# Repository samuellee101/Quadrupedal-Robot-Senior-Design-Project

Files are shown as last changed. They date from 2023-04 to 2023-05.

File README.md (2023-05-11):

# Quadrupedal Robot with the aim of Obstacle Avoidance using Artificial Intelligence
UTRGV - University of Texas Rio Grande Valley

Hello, my name is Samuel Lee, and together with my fellow teammmates Ryunghoon Ahn, and Christian Valdes, we aimed to have a quadrupedal robot walking by the end of our senior design project. The eventual goal of this project was to have a walking quadrupedal robot that moves using Artificial Intelligence, and is able to avoid obstacles (walls, buckets, basketballs), however, for the purposes of our senior design project, we wanted a walking quadrupdal robot.

This is meant to be a repository to show to future students working on this project, with helpful files to guide these students.

The quadrupedal robot was built using a combination of 3D printed parts using UTRGV's engineering building print labs, servos/wires/Jetson Nano purchased online, and was constructed in the Artificial Intelligence lab at UTRGV.

Ryunghoon Ahn was responsible for the physical construction of the robot. This includes soldering/screwing parts and ordering electrical parts online.

The file 'gazebo/spot_mini_mini' has work that Christian and Ryunghoon did in order to make the robot run in simulations.

The file 'gyroscope' details work that Samuel did in order to get the gyroscope up and running.

The file 'midterm-presentation' shows what we presented during our midterm presentations, and the powerpoint within details our progress halfway through this project. Joint Christian/Samuel effort.

The file '3D-printed-instructions' details work that Samuel did in order to get the 3D printed parts necessary for the project.

'End-of-Semester-Deliverables' has our final report and final presentation.

Christian and Ryunghoon are responsible for the simulation aspect of this project.

The robot itself is able to move its legs with the help of the servo. Video/Images will be included in the final presentation.

We would like to thank Christian Narcia from the Artificial Intelligence labs for the files found in 'revised-stl-parts.'

Special thanks to Dr. Dongchul Kim for being our project overseer, and Dr. Noe Vargas for his patience at the Makerspace 3D print lab. Thank you Dr. Erik Enriquez for helping us with the simulation.

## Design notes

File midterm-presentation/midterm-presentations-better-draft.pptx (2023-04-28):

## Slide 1

Obstacle Avoidance With a Quadrupedal Robot

Ryunghoon Ahn, Samuel Lee, Christopher Valdes, Dr. Dongchul Kim
Department of Computer Science, College of Engineering and Computer Science

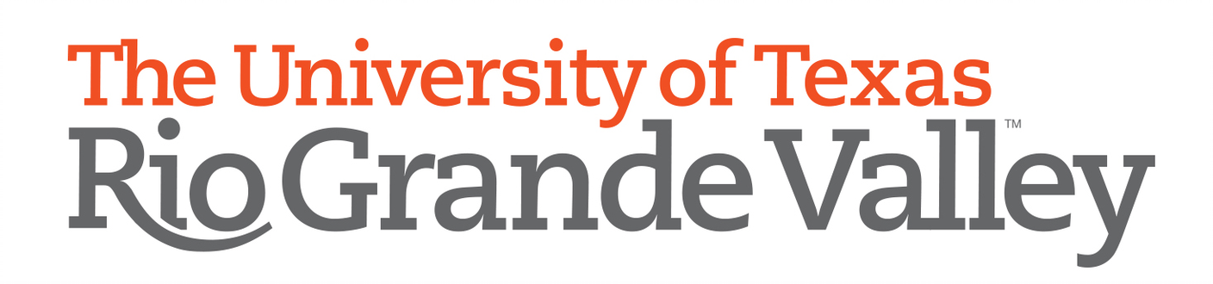
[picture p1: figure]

INTRODUCTION
Abstract
This project revolves around a quadrupedal robot that does usage of a JetsonNano to implement neural network computations for the robot so that it can perform actions autonomously.
Introduction
There are three main components for this project. First is the creation of the real robot, second is the simulation of the robot, and third is Sim2Real which refers to the transferring of the simulation gathered information to the physical robot.
Components for the physical robot are the Jetson Nano, 12 35.6kg 7.4~8.4 Servos, PCA9685 Servo Driver, MPU6050 Gyro, and HC-SR04 Ultrasonic Sensor. The main body of the robot is composed of 3d printed parts.
Choosing the ideal software to perform our simulation was important as a lot of these simulation environments are not supported by the Jetson Nano. After some research we decided on using ROS(Robot Operating System)/Gazebo which is known for smoothing out the transfer of simulations to real robots. For the reinforcement learning aspect we intend to employ tensorflow into the simulation.
For the senior project deadline, we wish to have the physical robot move in a straight line not with a controller, but with our program.

GOALS
Our immediate goal was creating a working robot that moved with circuitry, 3d printed parts, and attached devices like a front facing camera. We also aimed to have at least some simulations of the robot learning to walk. Throughout the project, we wanted to gain industry knowledge.
- Assembly of a working, functioning quadruped.
- Gain experience with robotics and robot simulators.
- Hands on learning approach, physical end product.

Lots of circuitry involved.

METHOD, PLAN or APPROACH
Details, Details
Initially, we had a way smaller robot we were going to use.
Here’s a picture of the back plate of the previous robot:
3D printed parts were printed in the Makerspace at the engineering building lab. Circuitry/servos were purchased online. Assembly was done in the research lab.
The software aspect of the project had many unexpected roadblocks. Initially, we had established that we would use Isaac Gym as our simulation environment but realized the Jetson Nano would not be able to handle it.
After some research, we settled with ROS/Gazebo which the Jetson Nano can handle. Started by importing the robot and spawning it to the Gazebo environment, then learning all about ROS and how to take control of the robot’s movement. Our two language options to write our scripts for the robot on ROS/Gazebo were Python and C++ and we stuck with Python. Writing our Python scripts we can control ROS/Gazebo.

Gazebo simulator. Notice the addition of a front-facing camera.

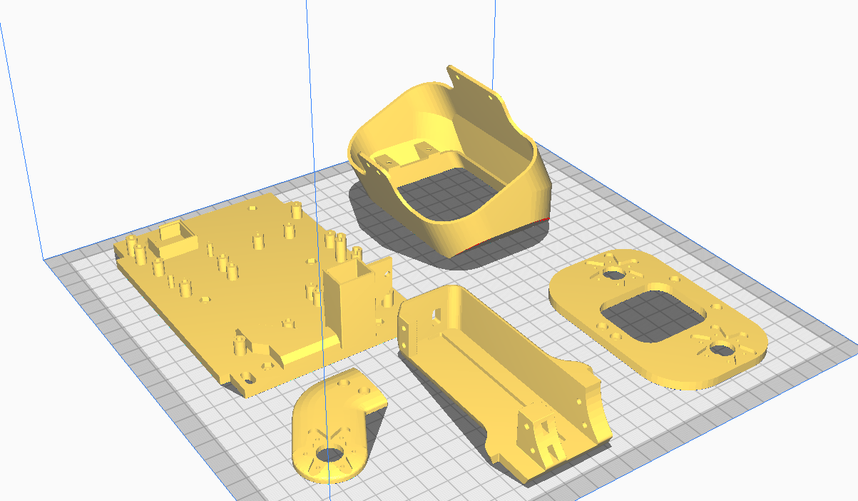
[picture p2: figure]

RESULTS or PROGRESS
We’ve accomplished quite a lot already.
Here is a quick rundown:
- ROS/Gazebo/Tensorflow installation in Ubuntu.
- Procurement of circuitry, sensors, motors.
- 3d printed close to 100 parts (not all of which were used).
- Comfortable with Robot movement in ROS/Gazebo.
- Constructed a plastic/metal robot.
- Optimized parts, for example the feet of the robot are in a more flexible material (TPU). Some parts needed infill increased as well.
- Calibrated all servos to not go past allowed degrees
- Calibrated Ultrasonic Sensor
These are examples of parts we don’t use anymore:

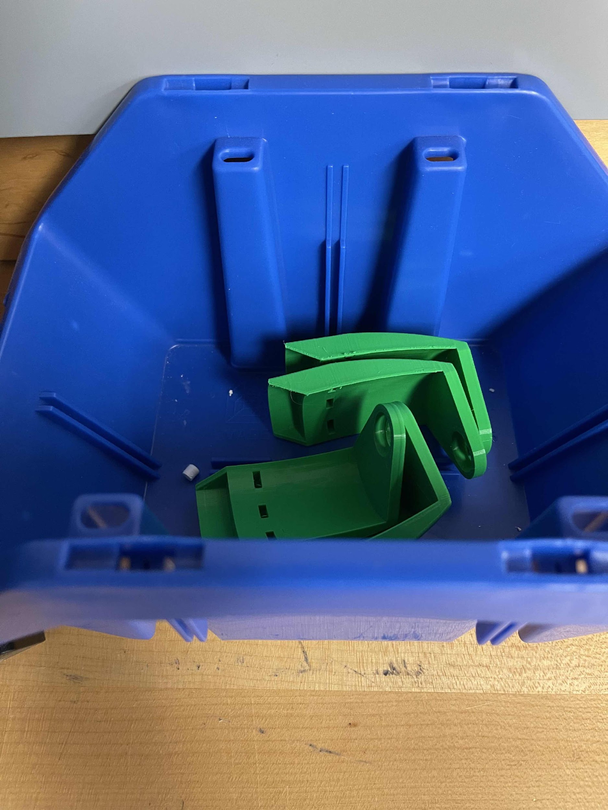
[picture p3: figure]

Not enough infill

DISCUSSION
About Printing
The Makerspace was essential for this project. Thanks to the help of the engineering building/department and more specifically Dr. Noe Vargas, we were able to print the 3d printed parts necessary for this project.
Thank you Dr. Vargas!
About The Robot
We are able to move all servos and gather data from sensor on the robot such as the camera. We are also at the stage where our main focus is no longer on robot construction/assembly but on the the elaboration of our NN model and the transferring of it to the physical robot.
Once we have created a learning model that we are satisfied with in the simulation, we will have to employ it to the physical robot which is where ROS comes into play. ROS has embedded libraries that aid with the transfer of information from a simulation to actual circuitry and sensors of a robot.

CONCLUSIONS
We’ve made good progress, but we are not content with what we’ve done so far so now our next immediate goal is getting the physical dog walking with a learning model which can be daunting but we believe is possible.
Next steps:
- Continue programming, robot should be able to walk in a straight line through model.
- Robot does not fall over in either the simulator or in physical trials.
- Extra parts/materials in case a part is damaged.

ACKNOWLEDGEMENTS
Thank you again Dr. Vargas for the aid in 3d printing, and the Teaching Assistants in the Makerspace. Thank you Dr. Kim for the advice and opportunity to do this in the first place. Thank you to the research lab members who helped us with this project as well.

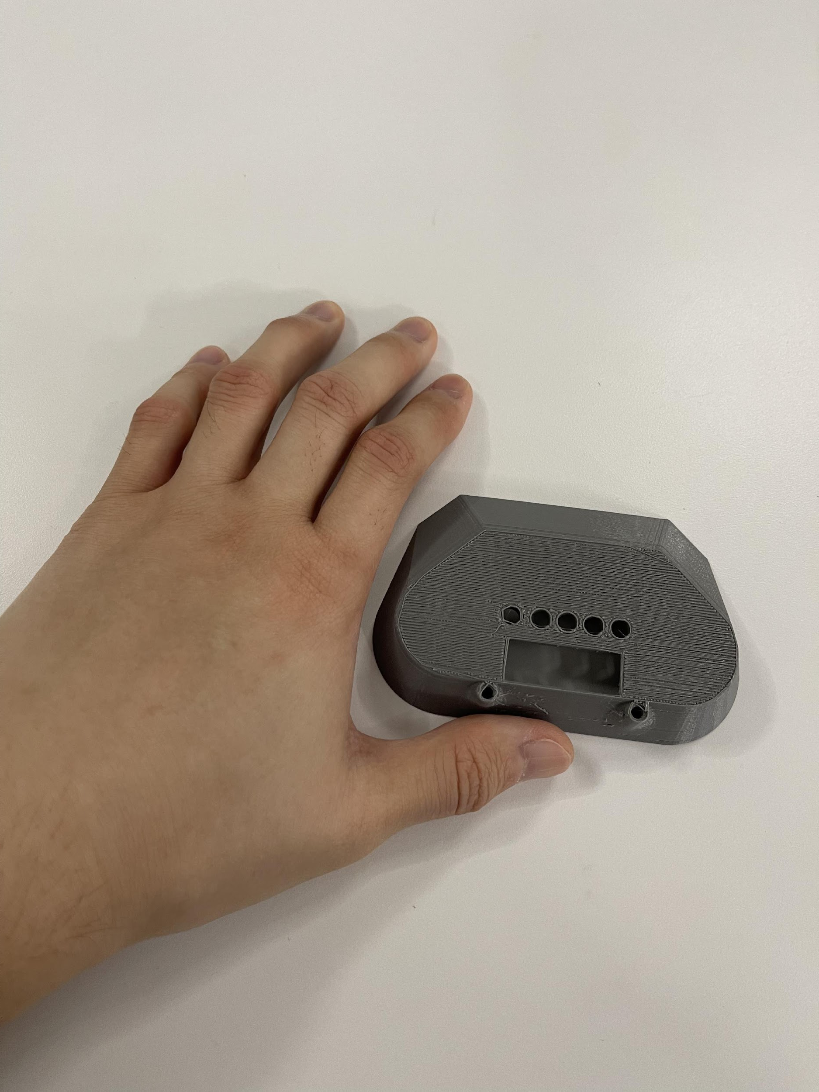
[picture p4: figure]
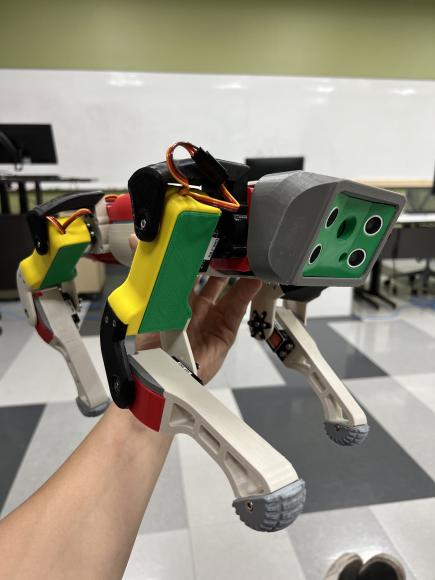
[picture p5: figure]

Completed robot construction using 3d printed parts.

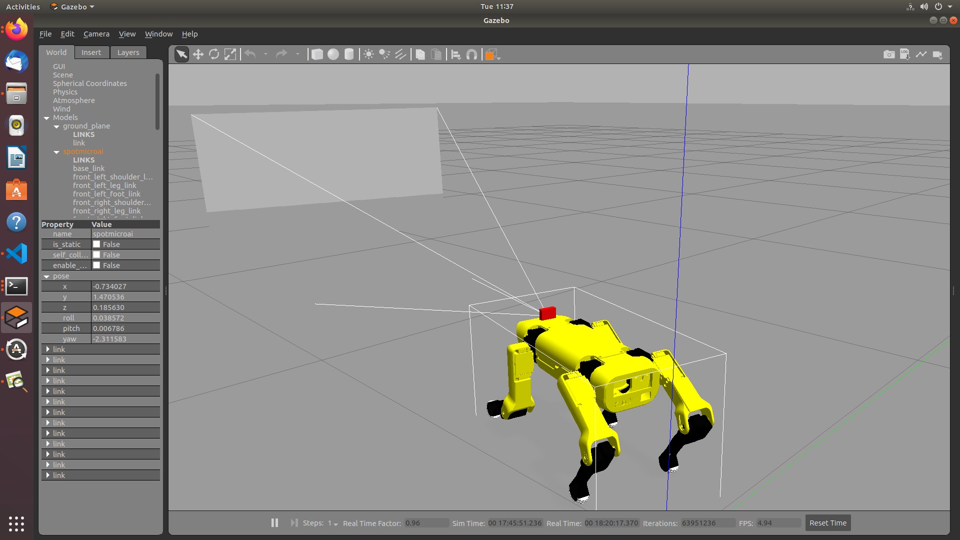
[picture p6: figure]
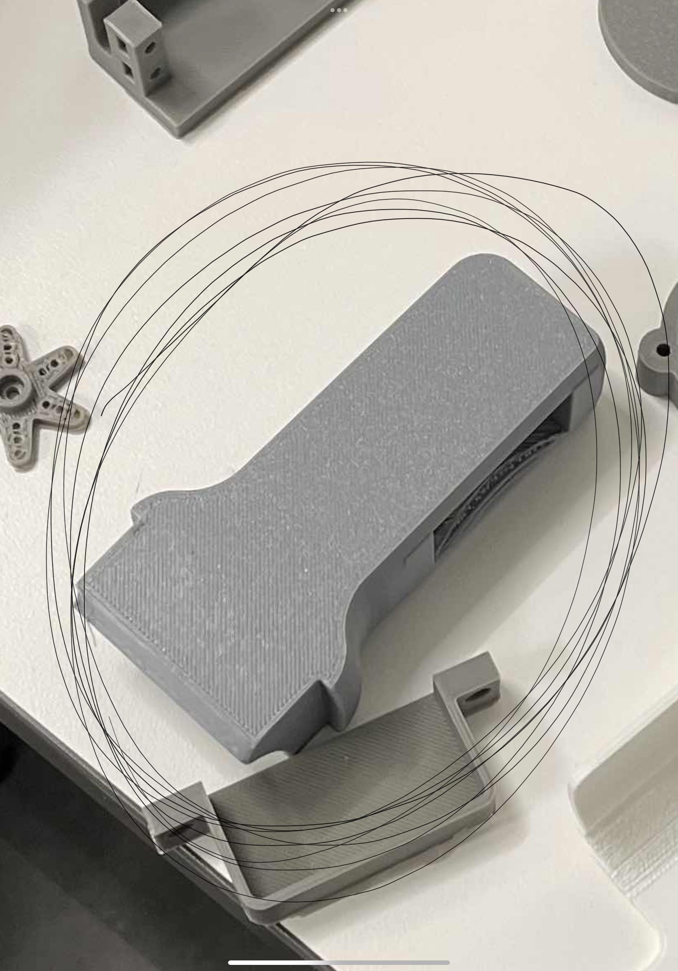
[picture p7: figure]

Wrong material (TPU)

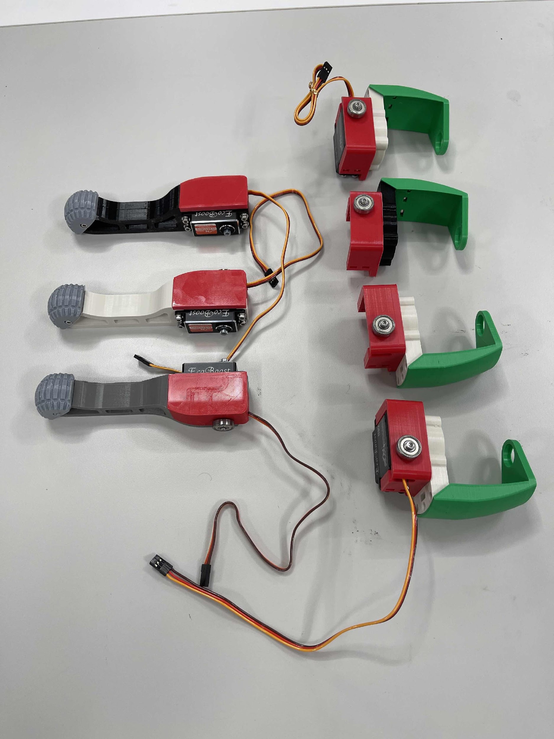
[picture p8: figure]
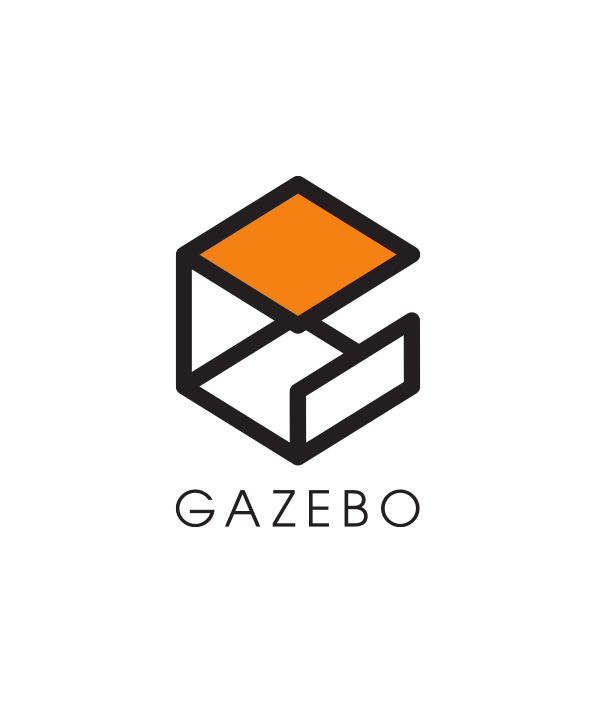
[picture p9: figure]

Gazebo/ROS

Ultimaker Cura Slicer

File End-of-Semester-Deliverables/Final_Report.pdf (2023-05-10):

Quadrupedal Robot

Senior Design Project

Ryunghoon Ahn, Christopher Valdes, Samuel Lee

Students

University of Texas Rio Grande Valley, Edinburg, Texas, 78539

Dr. Dongchul Kim

Supervisor

University of Texas Rio Grande Valley, Edinburg, Texas, 78539

In the field of robotics, there is an ongoing effort to utilize artificial intelligence to

perform obstacle avoidance. During the Spring 2023 semester, our team hoped to start research

into this field, by first constructing a quadrupedal robot and then programming this quadrupedal

robot to move in a straight line. Furthermore, documentation in the github repository is meant to

help future students, who build upon our knowledge in the future.

Most computer science programs focus on software, theoretical math, and programming.

However, some fields of research require hands-on experience with hardware. In this project, by

building, testing, and writing code for a quadrupedal robot, our team aimed to gain hands-on

experience with not only hardware, but how this hardware integrated with the software

component of our quadrupedal robot.

Boston Dynamics has already created quadrupedal robots, such as their Spot robot, which

is able to navigate terrain and even stand upright after being flipped over. However, the

extremely high financial cost for robots such as Spot may not be an option for every research lab

or university. Our quadrupedal robot, using 3D printed parts and other electronics such as a

Jetson Nano and jumper wires, aims to have a cost effective yet fully functional robot capable of

being used as research into obstacle avoidance and artificial intelligence.

Our end goal for this semester was to have a walking quadrupedal robot that is able to

move in a straight line using servos, a jetson nano, and 3D printed parts. The 3D printed parts

were printed at the Makerspace lab in the engineering building of UTRGV (University of Texas

Rio Grande Valley). Electronic parts were purchased using funds from the Artificial Intelligence

department, as were tools, batteries necessary for robot construction. Pybullet simulator was used

to program the robot to move.

During the end of April, our team managed to make the robot stand upright using servos. Here is

a video demonstrating this fact:

https://youtube.com/shorts/rAv_qdHrh14?feature=share

In this video, you can see the servo leg extending.

https://youtube.com/shorts/udVggbsvQW4?feature=share

In this video, you can see the servo leg retracting.

https://youtube.com/shorts/w0CVjQnS3aU?feature=share

In this video, you can see the robot standing up from its resting position.

https://youtube.com/shorts/45N6XMv1CY0

In this video, you can see the robot moving all legs in a walking motion.

Instead of the Issac Gym simulator, our team chose to work with the Gazebo simulator as

the Gazebo simulator has Robot Operating System (ROS) support. ROS libraries and tools were

helpful in the running of the quadrupedal robot simulations. One trade off was that less

information, guides, and helpful informational threads were available for Gazebo, although

plenty of documentation and similar support were readily available for Gazebo. We also used the

Jetson Nano as our main computer for the robot, which is less beginner friendly than Arduino,

but is able to run Linux and is essentially a fully functioning computer.

Towards the end of the semester, we also used Pybullet, which allowed us to simulate

both soft and rigid body dynamics. We were unable to implement OpenAI within the time frame

allotted for this project, so instead we took inspiration from the previous quadrupedal robot

communities who worked on this project and used Pybullet to determine which policies our

simulation should use. This helped us figure out which policies to use in our Gazebo and ROS

implementation.

Q-learn was the first algorithm we started with. This algorithm seemed like a promising

reinforcement learning algorithm, which chooses actions at random and maximizes reward.

However, Q-learning does not fit the scope of our project, and requires us to know specific states

which is not feasible with the massive scope of our project.

The next algorithm we tried was Double Deep Q-Network (DDQN). DDQN uses two

neural networks, one to select the best action and the other to estimate its value. By doing this,

we prevent overestimation of Q-values, which leads to bad policies. A policy is a mapping from

states to actions that an agent follows during environment interaction. The policy determines

what action the agent should take to get the maximum reward. So DDQN allows us to avoid any

bad mapping, essentially. The target network is frequently updated to match the online network,

which helps the learning process.

The final algorithm we would like to cover in this report is Proximal Policy Optimization

(PPO), a reinforcement learning algorithm that finds the best policy for an agent interacting with

an environment. PPO updates the policy by maximizing the expected reward, while limiting the

update to be within a trust region. This prevents the agent from doing anything risky. This

constraint is achieved by using a surrogate objective function that calculates the true objective

function within the aforementioned trust region.

Reinforcement Learning is all about testing and trials. We tested that our controller was

actually connected to the joints of the robot in the simulation, which allowed us to ensure that the

joints worked correctly. It was also important to ensure that the physics within the environment

were correct. Finally, all of the parameters have to be perfect to make a reinforcement learning

simulation work. Some examples include set actions, observations, rewards, and constraints.

Our team did not have a strict weekly schedule. Tasks were assigned based on

completion. We laid out what each teammate was responsible for at the beginning of this project,

although even this was flexible and subject to change. In short, the schedules for all three

teammates changed according to progress made with the project.

Initially, Ryunghoon would focus on the procurement of parts for, and the assembly of,

the quadrupedal robot. Samuel would focus on 3D printing. Christopher would focus on

researching different simulators, and installing, running, and learning how to program in Gazebo.

Then, Samuel completed 3D printing and worked on implementing the gyroscope.

Ryunghoon successfully completed robot construction. Christopher was able to successfully get

the robot to stand up using servos. Ryunghoon began working on the simulation after completion

of the quadrupedal robot. Christopher also focused his efforts on the simulation. Then, Samuel

finished the gyroscope implementation and worked on gathering documentation, and the final

report. All members contributed to the final presentation.

We must emphasize that there was a lot of back and forth help between teammates, and

even help requested from other people within the department. When we discovered that the stl

files had to be modified, Christian Narcia, a fellow student in the Artificial Intelligence lab,

helped modify these files for us. Christopher was able to print a few of the smallest parts that

were not printing correctly at the engineering building, using his friend’s 3D printer. Samuel also

researched both the simulators and simulation, and information was shared between all three

teammates constantly.

Additionally, since work was divided into sections that did not overlap at the start, for the

first half of the semester, each teammate was assigned a task different from other teammates, so

there was not really inefficient overlap. Later in the semester, to avoid unnecessary overlap and redundancy, Samuel focused on documentation/presentations, and Ryunghoon and Christopher

worked on the simulation. Even then, initially Ryunghoon worked on a simulation without ROS,

and Christopher worked on a simulation with ROS.

Discord was used in order to both communicate between teammates and communicate

with the professor. “MI@UTRGV” was the research lab’s official discord channel, where the

team could communicate with other students in the research lab. Whenever a teammate had a

question for anyone, discord was the best method of communication besides in person

conversations.

Schedules of all teammates tended to change based on what was needed from each

teammate. For example, programming the quadrupedal robot to move was a lot more difficult

than anticipated, so for our weekly presentation on April 21, 2023, we moved our planned

presentation on the robot back a week, and focused instead on presenting the gyroscope and

progress made on the simulation. Our schedules and timetables changed constantly given the

current state of progress with this project.

One major change to this project was right at the start of the project. Our team realized

quickly within the first week of the project that it was impossible to build a quadrupedal robot,

program it to move with simulators, incorporate Artificial Intelligence, and then use that

Artificial Intelligence to avoid obstacles all in a single semester. A more feasible yet still

challenging goal of having the quadrupedal robot completed and be able to move its servos using

our simulation was agreed upon.

Secondly, Samuel originally printed a much smaller robot during the winter of the year

2022. However, we decided on a larger robot using another Thingiverse project that was able to

house more electronics and circuitry. So, all the original parts for the smaller robot had to be put aside for any future use, and Samuel re-printed the robot during the first few months of Spring

2023.

Both Gazebo and the Jetson Nano are complex, powerful tools capable of bringing this

project to life. However it was because of this complexity that progress with programming was

slow, as there was both a lot of research that had to be conducted and a wide array of knowledge

needed before programming could begin. For this reason, it is highly recommended that future

students look into and research Gazebo, the Jetson Nano, ROS, and python extensively before

picking up this project.

Neither Artificial Intelligence or obstacle avoidance could feasibly be implemented into

the quadrupedal robot given our small timeframe. So our team was right to focus instead on a

working walking quadrupedal robot. Now, the quadrupedal robot is able to move thanks to the

Pybullet simulation, and we have left documentation, a simulation, and the physical robot for

future students to work off of and improve.

A project management obstacle we ran into was near the end of the semester. After spring

break, we wanted to spend half of our remaining time on the simulation and the latter half on

using the code from the simulation to make the robot move by itself. After trying both Issac Gym

and Gazebo simulators, we decided instead to work with the Pybullet simulator. This simulator

allowed us to finally get a working simulation, and helped us with the robot moving

demonstration shown in the earlier videos.

Teamwork was absolutely essential, as Samuel and Christopher had to work together to

get a few small pieces 3D printed, Christopher and Ryunghoon shared information and ideas

about the simulation, Samuel and Ryunghoon communicated back and forth to ensure that

Ryunghoon had all the 3D printed parts necessary for assembly. These are just a few examples of

many where teamwork was essential for this project.

There is always going to be a difference between what you see in a computer and how

that translates into a real life scenario. 3D part files that seemed like they would print perfectly

took two or even three tries to get right. Helpful guides on the internet cannot account exactly for

what you are trying to do, as evidenced by the fact that the team had to learn firsthand that the

Jetson Nano, by itself, could only connect to one SCL/SDA dependent device at a time. Even

youtube videos of talented programmers showing a complete simulation of a walking robot did

not translate exactly into code we could use, as our robot did not have the same exact

parts/orientation, or we ran into other difficulties. For a more specific example, Samuel

constantly had to change splicer settings and model layout during 3D printing to avoid bad

prints, as some prints were disfigured or unusable and had to be reprinted. However, despite all

of this, we managed to fulfill most of our original goals and have left documentation, simulation,

and the physical quadrupedal robot for future students.

Bibliography:

Addison. “Visualize IMU Data Using the MPU6050, ROS, and Jetson Nano”

automaticaddison.com, April 19, 2021. https://automaticaddison.com/visualize

-imu-data-using-the-mpu6050-ros-and-jetson-nano/.

Kim, Deok-yeon. “SpotMicroAI.” spotmicroai.readthedocs.io, N.d. https://spotmicroai.

readthedocs.io/en/latest/.

Kubina, Michael. “SpotMicroESP32.” github.com, June 1, 2021. https://github.com/

michaelkubina/SpotMicroESP32.

Martínez, Joël. “Ros Based Control With Gazebo Simulation For SpotmicroAI” gitlab.com 2021.

https://gitlab.com/public-open-source/spotmicroai/simulation/-/tree/master/UserJo%C3%

ABl%20Martinez.

Nicrusso. “Rex: An Open-Source Quadruped Robot.” github.com, May 15, 2021.

https://github.com/nicrusso7/rex-gym.

Parrilla, Miguel Ayuso. “DIY Hobby Servos Quadruped Robot.” hackaday.io, June 5, 2020.

https://hackaday.io/project/171456-diy-hobby-servos-quadruped-robot.

Schoeffer, Michael. “Tutorial: How to use the GY-521 module (MPU-6050 breakout board) with

the Arduino Uno.” mschoeffler.com, October 5, 2017. https://mschoeffler.com/2017/

10/05/tutorial-how-to-use-the-gy-521-module-mpu-6050-breakout-board-with-the-arduin

o-uno/.

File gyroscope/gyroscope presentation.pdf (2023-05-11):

# Gyroscope on Robot

# Samuel Lee, Christian

4/7/23

# Physical component

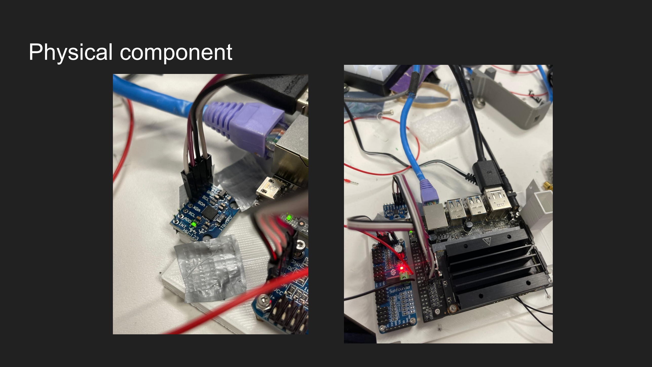
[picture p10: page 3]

# Need more SDA/SCL pins (previously sunfounder)

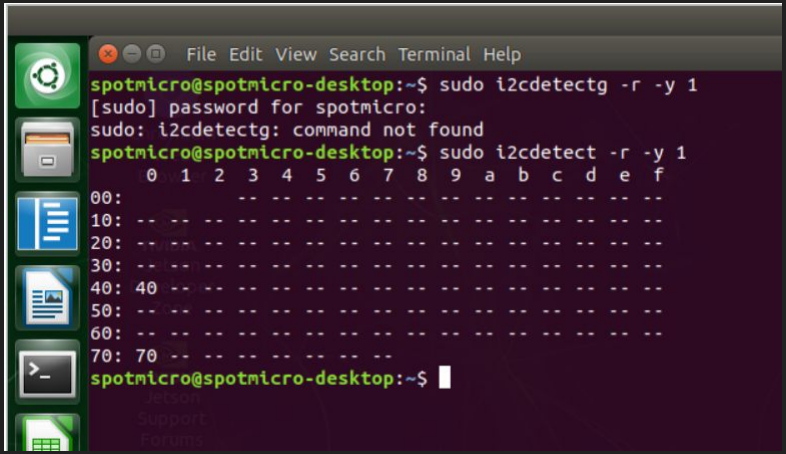
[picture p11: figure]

# Test adafruit blinka repository (code source in final slide)

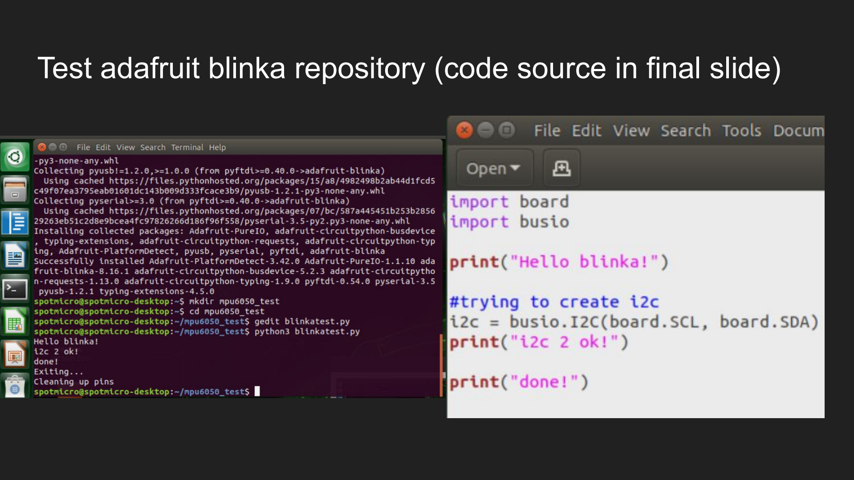
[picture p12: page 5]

# Second test program - temperature, acceleration, etc

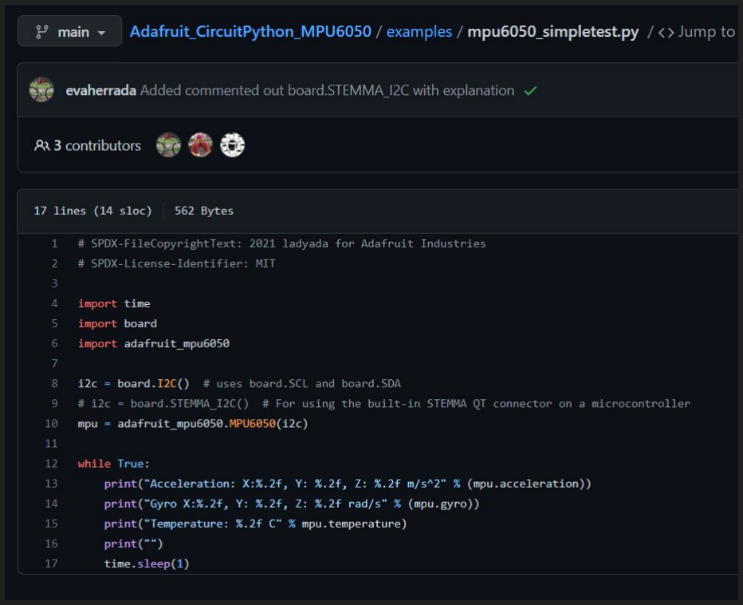
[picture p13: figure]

# tried: python3 mpu6050_simpletest.py

Traceback (most recent call last):
File "mpu6050_simpletest.py", line 10, in <module> mpu = adafruit_mpu6050.MPU6050(i2c)
File "/home/spotmicro/.local/lib/python3.8/site-packages/adafruit_mpu6050.py", line 205, in __init__ self.i2c_device = i2c_device.I2CDevice(i2c_bus, address) File "/home/spotmicro/.local/lib/python3.8/site-packages/adafruit_bus_device/i2c_device.py", line 63, in __init__ self.__probe_for_device()
File "/home/spotmicro/.local/lib/python3.8/site-packages/adafruit_bus_device/i2c_device.py", line 185, in __probe_for_device raise ValueError("No I2C device at address: 0x%x" % self.device_address) ValueError: No I2C device at address: 0x68

# success

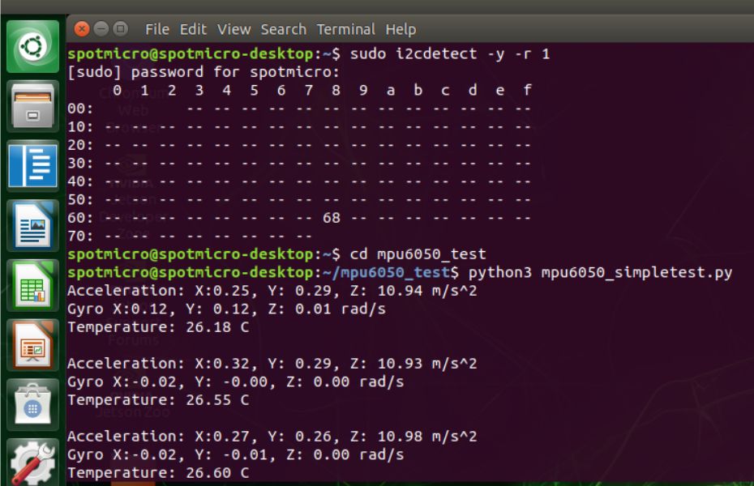
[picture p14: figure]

# Attempt to Connect to HC-SR04

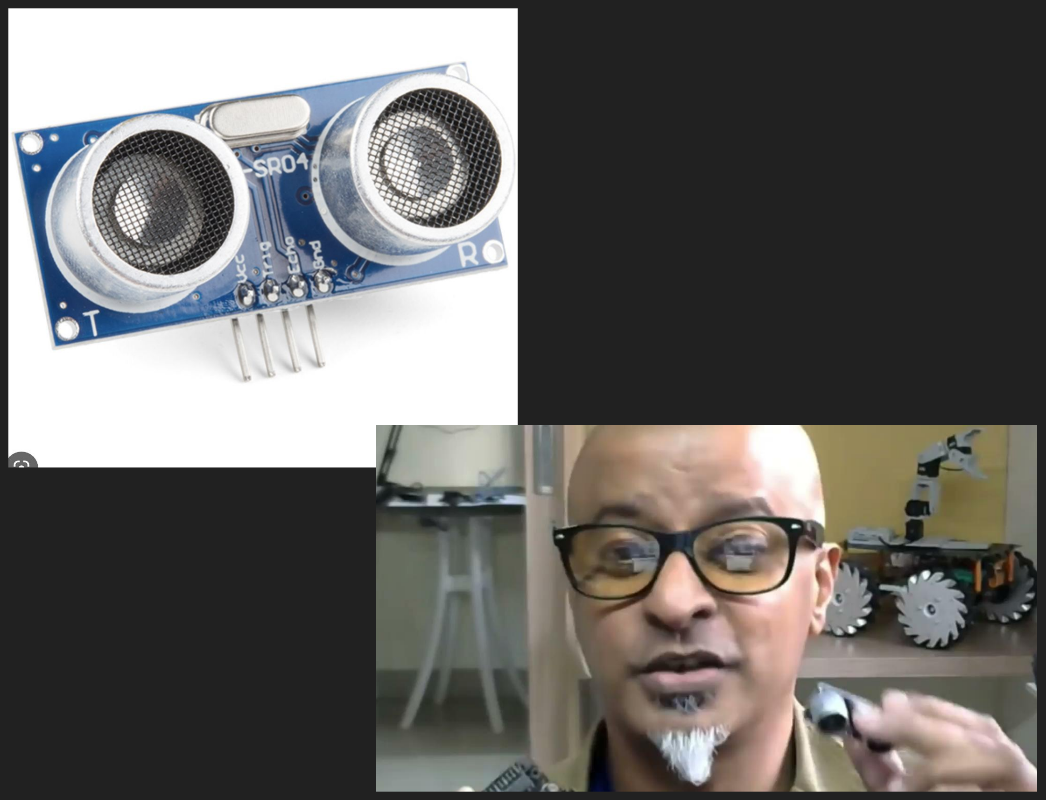
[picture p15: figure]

# Need parts to safely

add ultrasonic sensor.

# Regardless, have added ROS to Jetson Nano to get data from sensors and move servos with it

# Sources

# https://automaticaddison.com/visualize-imu-data-using-the-mpu6050-ros-and-jetso

n-nano/ (https://automaticaddison.com/visualize-imu-data-using-the-mpu6050-ros-and-jetson-nano/) - first test program, all commands/installation of gyroscope

# https://github.com/adafruit/Adafruit_CircuitPython_MPU6050/blob/main/examples/

mpu6050_simpletest.py (https://github.com/adafruit/Adafruit_CircuitPython_MPU6050/blob/main/examples/mpu6050_simpletest.py) - second test program

# both accessed 3/28/23

4/14/23

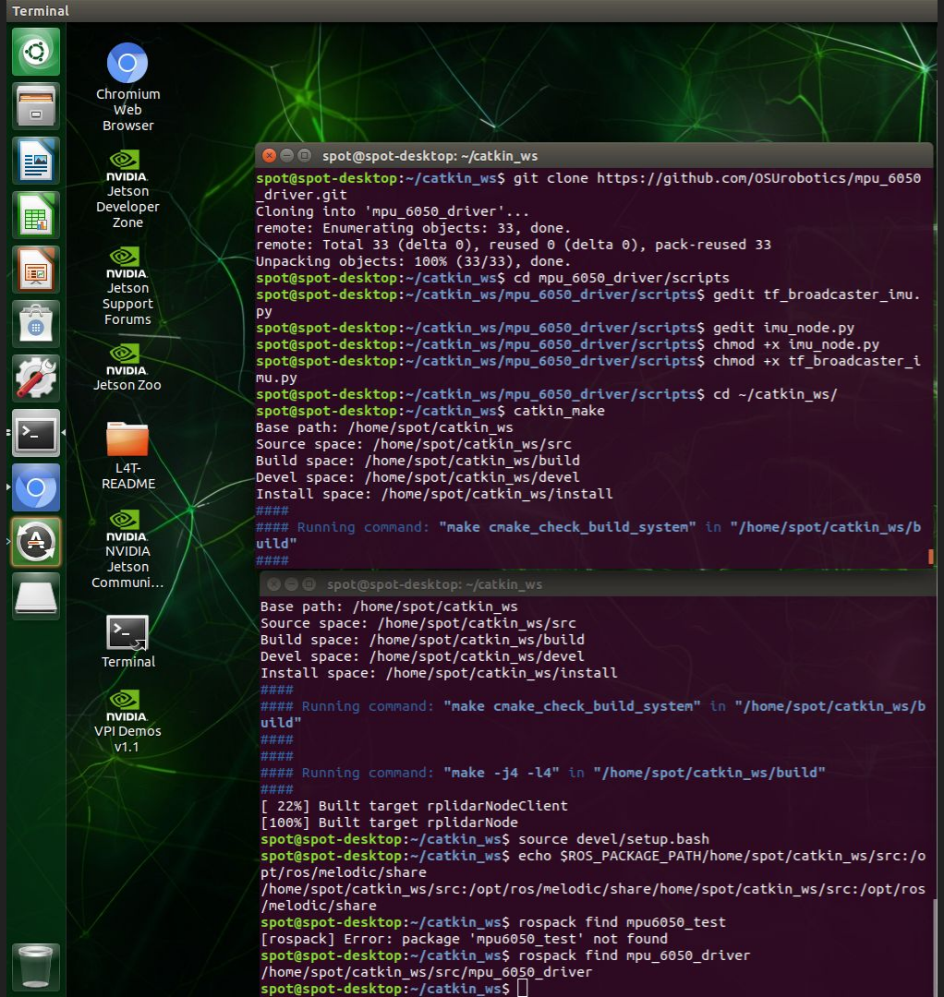
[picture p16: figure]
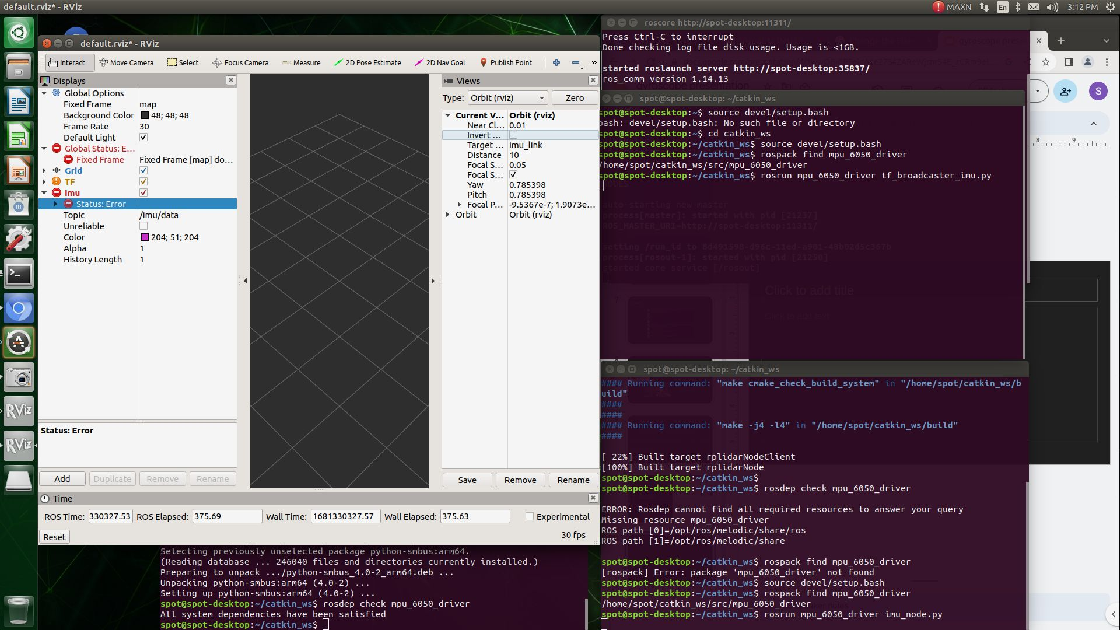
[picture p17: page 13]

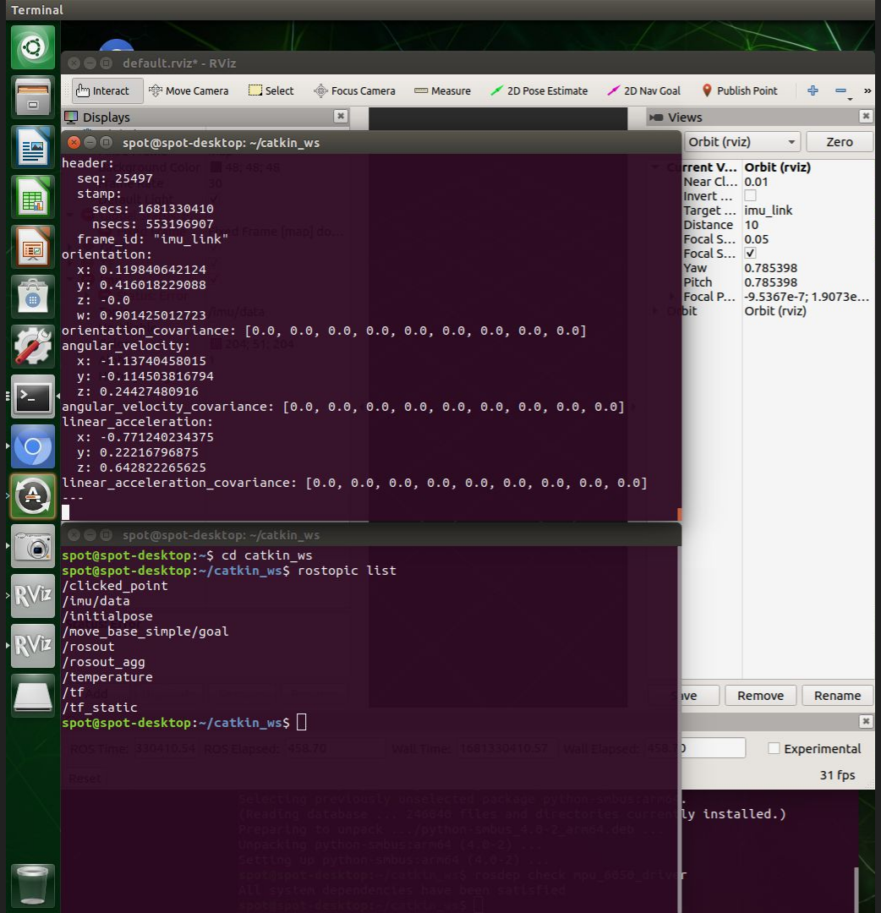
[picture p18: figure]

# Servos

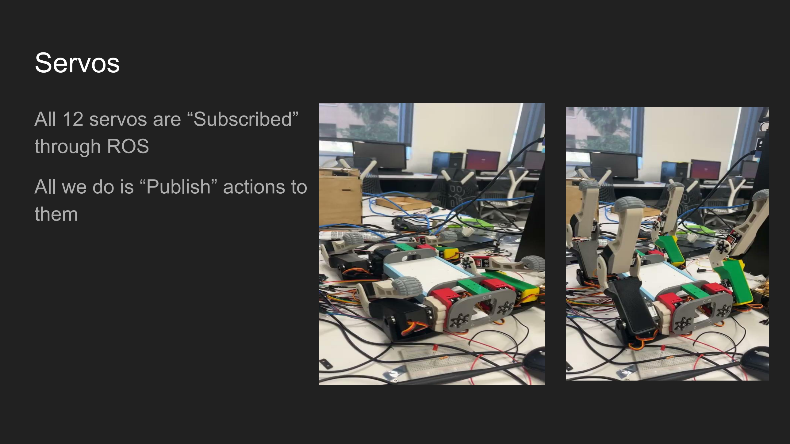
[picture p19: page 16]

# All 12 servos are “Subscribed” through ROS

# All we do is “Publish” actions to them

# Simulation

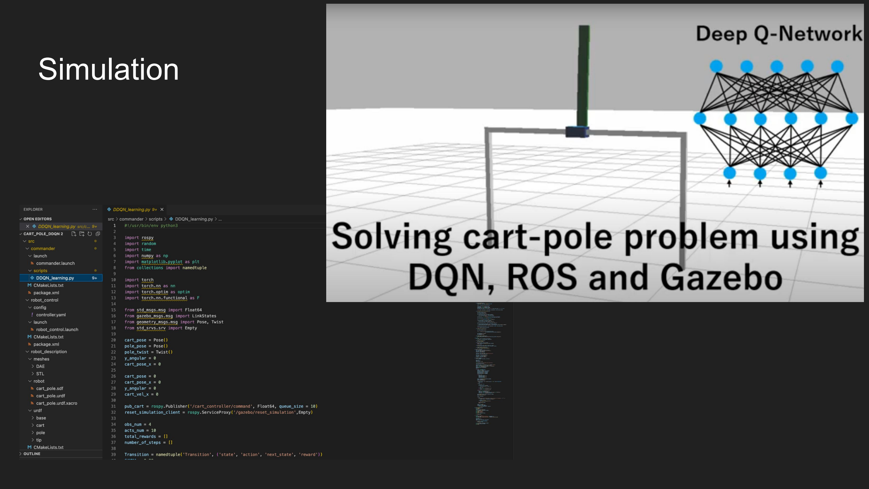
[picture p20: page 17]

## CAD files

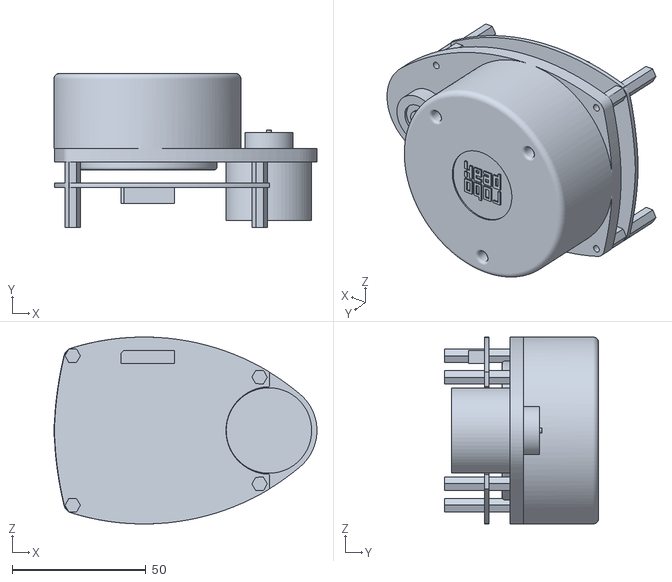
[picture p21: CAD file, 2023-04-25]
gazebo/spot_mini_mini/spotmicro/util/pybullet_data/assets/urdf/stl/rplidar_main.stl
98.5 x 57.7 x 70.0

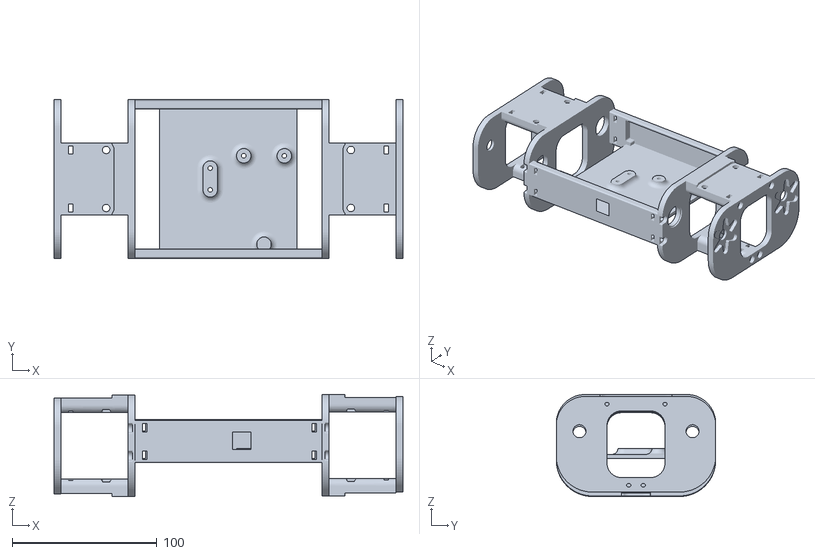
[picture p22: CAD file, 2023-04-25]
gazebo/spot_mini_mini/spotmicro/util/pybullet_data/assets/urdf/stl/mainbody.stl
240.7 x 110.0 x 70.4

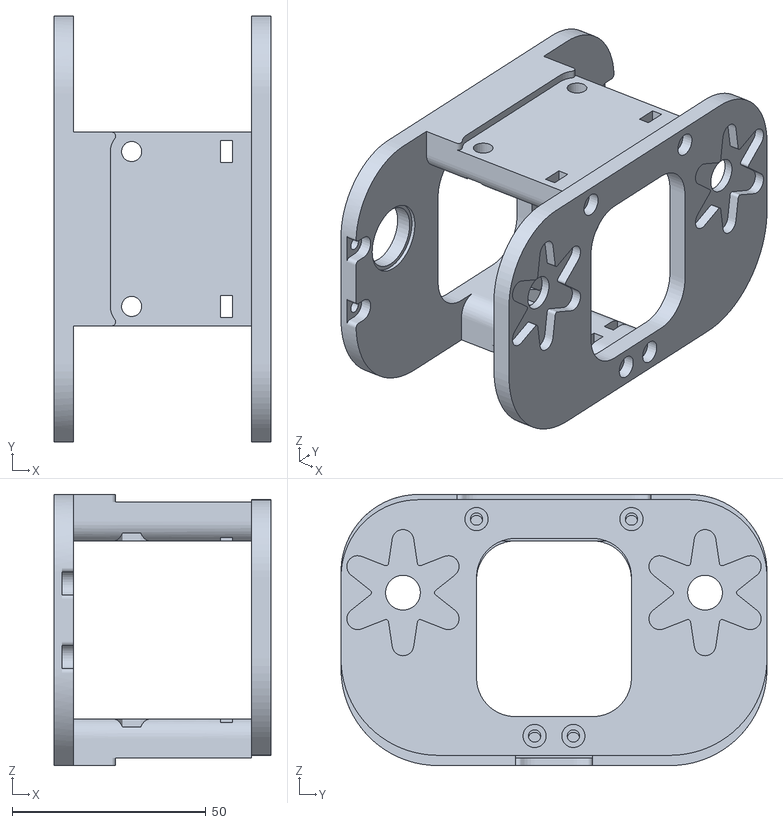
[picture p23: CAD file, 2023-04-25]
gazebo/spot_mini_mini/spotmicro/util/pybullet_data/assets/urdf/stl/rearmain.stl
55.9 x 110.0 x 70.0

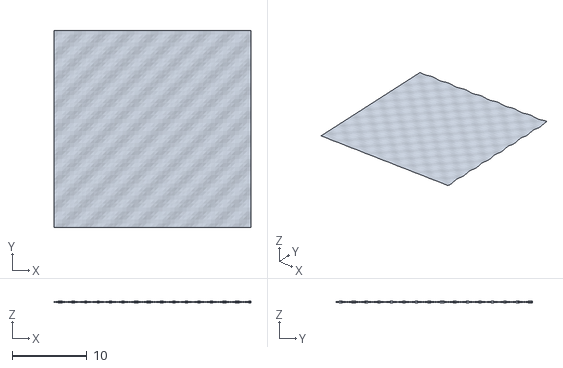
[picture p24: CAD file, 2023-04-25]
gazebo/spot_mini_mini/spot_bullet/src/mini_bullet/terrain9735.obj
26.3 x 26.3 x 0.24

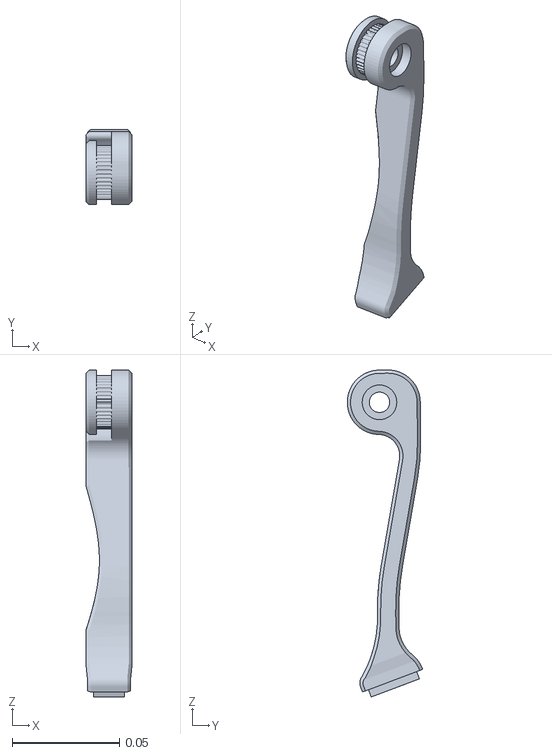
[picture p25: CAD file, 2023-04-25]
gazebo/spot_mini_mini/spotmicro/util/pybullet_data/assets/urdf/stl/OpenQuadruped/LEFT_LOWER_LEG.stl
0.0214 x 0.0351 x 0.152

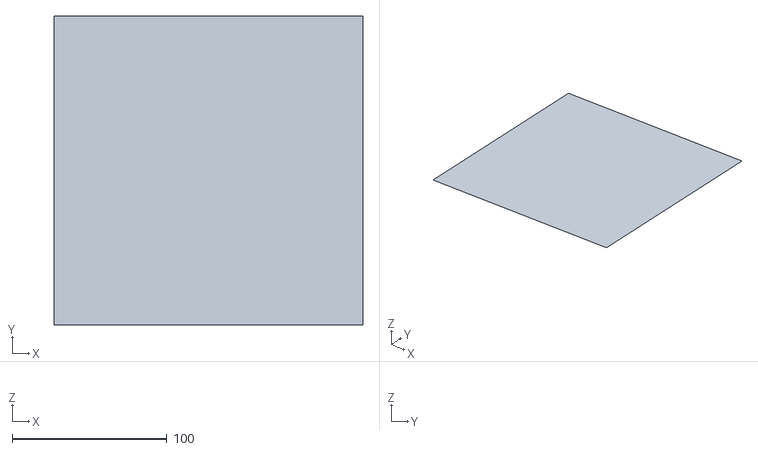
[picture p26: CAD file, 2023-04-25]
gazebo/spot_mini_mini/spotmicro/util/pybullet_data/plane100.obj
200.0 x 200.0 x 0

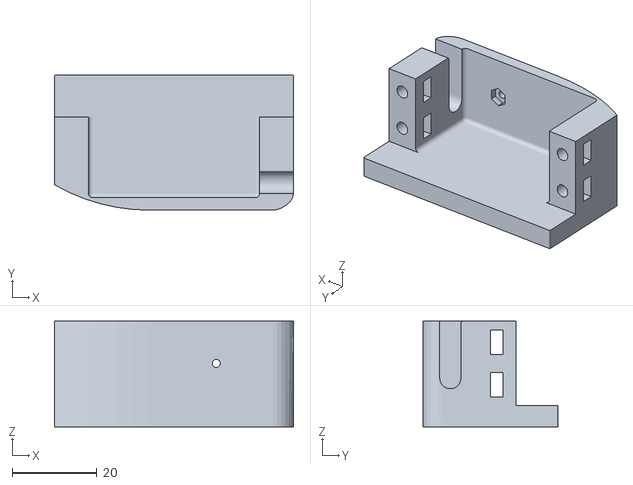
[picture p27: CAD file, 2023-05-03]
revised-stl-parts/Wrist__CounterpartRev.stl
56.5 x 32.0 x 25.0

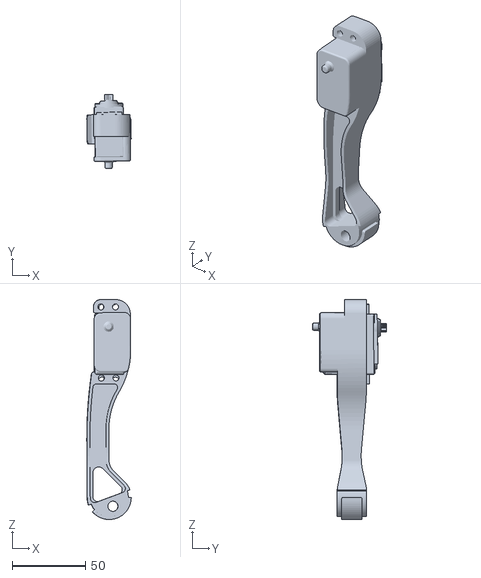
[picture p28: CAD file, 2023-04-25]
gazebo/spot_mini_mini/spotmicro/util/pybullet_data/assets/urdf/stl/lfoot.stl
30.4 x 50.7 x 150.0

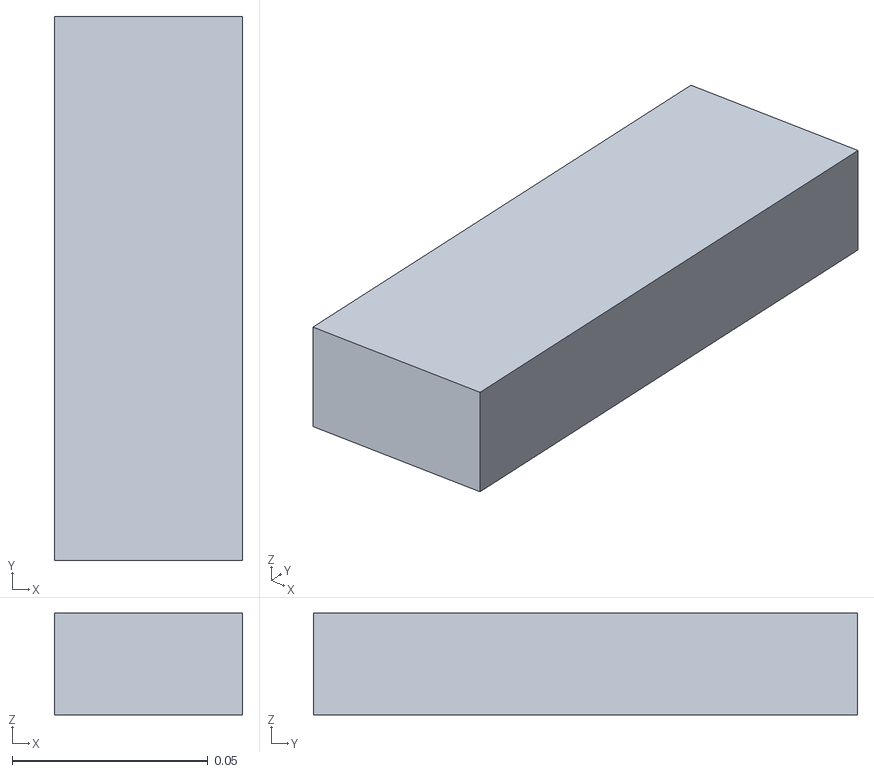
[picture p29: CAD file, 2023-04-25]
gazebo/spot_mini_mini/spotmicro/util/pybullet_data/assets/urdf/stl/OpenQuadruped/BATTERY.stl
0.048 x 0.139 x 0.026

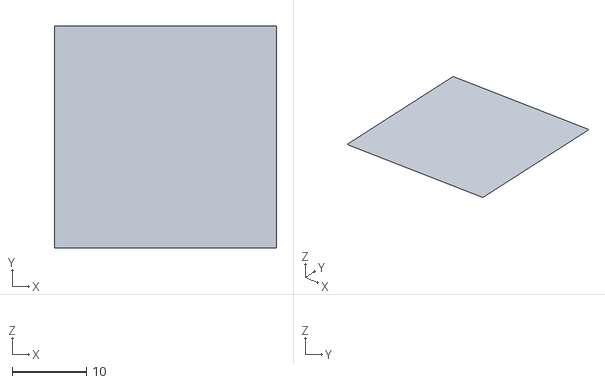
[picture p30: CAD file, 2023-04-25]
gazebo/spot_mini_mini/spotmicro/util/pybullet_data/plane.obj
30.0 x 30.0 x 0

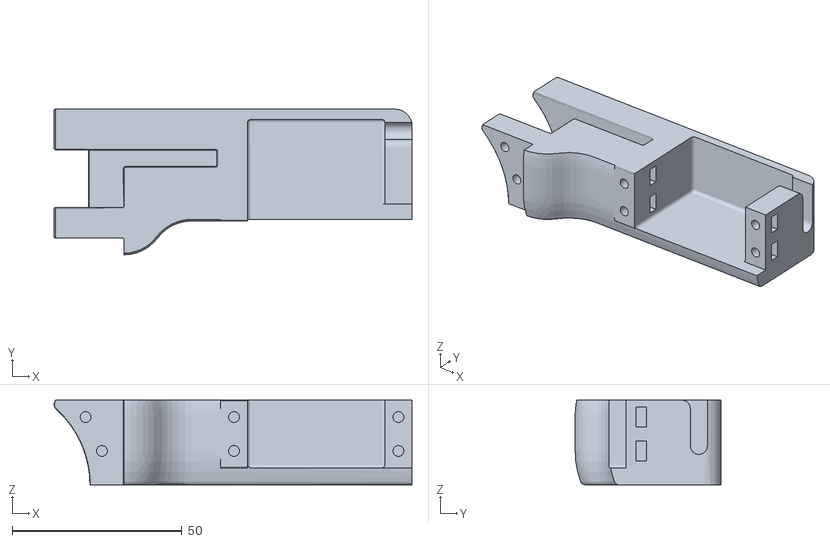
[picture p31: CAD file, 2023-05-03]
revised-stl-parts/Limb_Bottom_ShellRev.stl
105.6 x 43.0 x 25.0

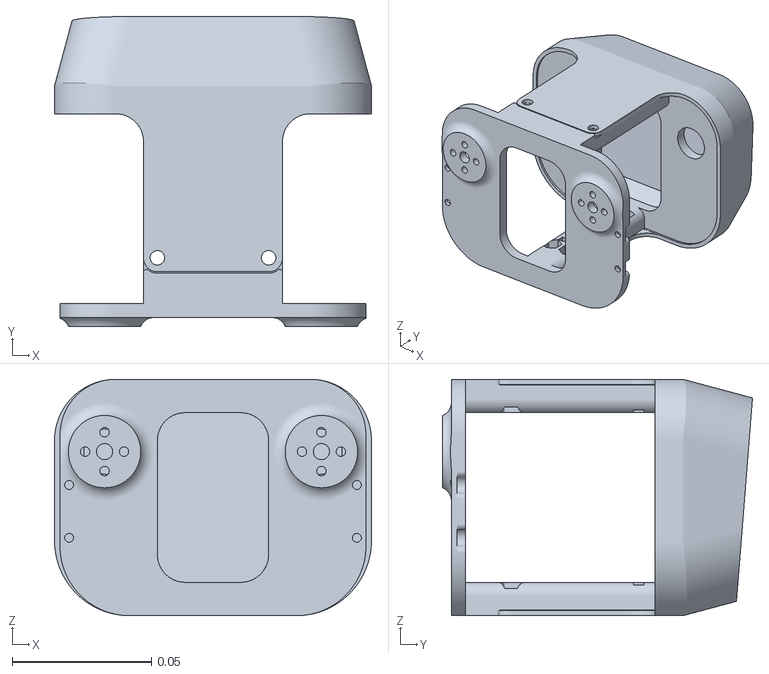
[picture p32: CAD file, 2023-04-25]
gazebo/spot_mini_mini/spotmicro/util/pybullet_data/assets/urdf/stl/OpenQuadruped/BACK.stl
0.114 x 0.112 x 0.085

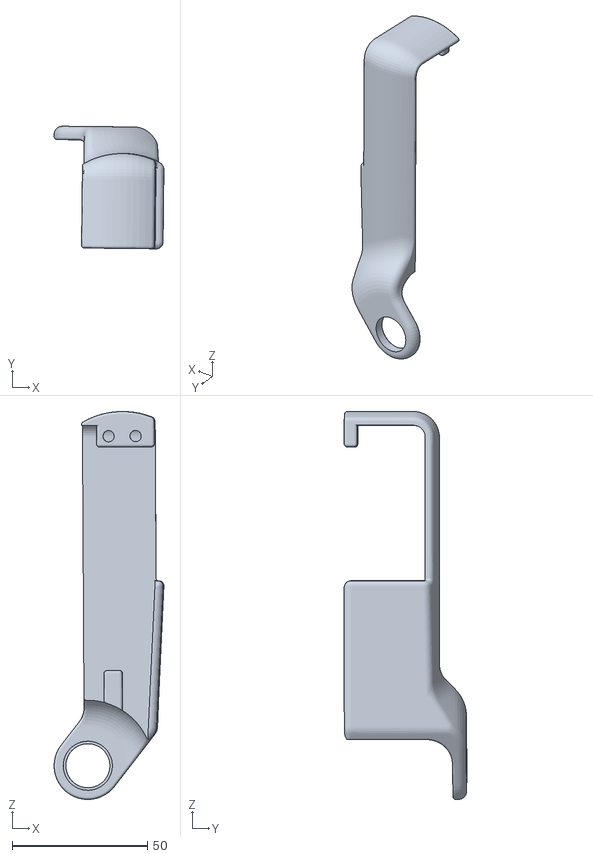
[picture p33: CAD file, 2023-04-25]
gazebo/spot_mini_mini/spotmicro/util/pybullet_data/assets/urdf/stl/rarm_cover.stl
40.7 x 45.4 x 143.6

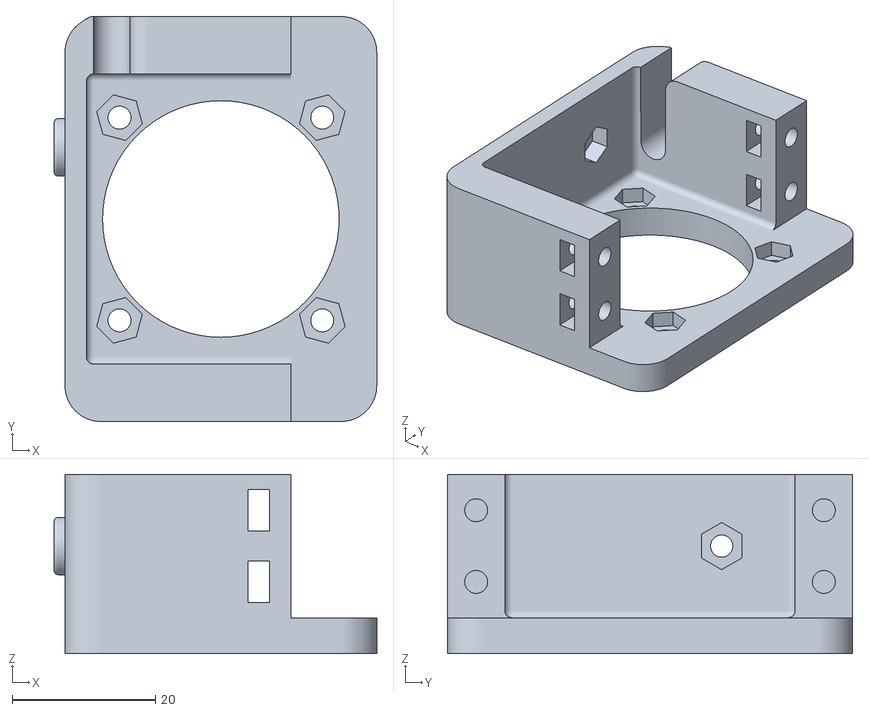
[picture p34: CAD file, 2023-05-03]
revised-stl-parts/Shoulder_Joint_Servomount_extended_BBRev.stl
45.0 x 56.5 x 25.0

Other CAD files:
gazebo/spot_mini_mini/spotmicro/util/pybullet_data/plane_transparent.obj
gazebo/spot_mini_mini/spotmicro/util/pybullet_data/assets/urdf/stl/OpenQuadruped/LEFT_FOOT.stl
gazebo/spot_mini_mini/spotmicro/util/pybullet_data/assets/urdf/stl/rfoot.stl
gazebo/spot_mini_mini/spotmicro/util/pybullet_data/assets/urdf/stl/OpenQuadruped/Chassis_Left_Side.stl
gazebo/spot_mini_mini/spotmicro/util/pybullet_data/assets/urdf/stl/OpenQuadruped/Back.stl
gazebo/spot_mini_mini/spotmicro/util/pybullet_data/assets/urdf/stl/OpenQuadruped/Back_Bracket.stl
gazebo/spot_mini_mini/spotmicro/util/pybullet_data/assets/urdf/stl/OpenQuadruped/Chassis_Right_Side.stl
gazebo/spot_mini_mini/spotmicro/util/pybullet_data/assets/urdf/stl/OpenQuadruped/FRONT.stl
gazebo/spot_mini_mini/spotmicro/util/pybullet_data/assets/urdf/stl/OpenQuadruped/Front.stl
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

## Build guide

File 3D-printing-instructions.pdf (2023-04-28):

This is an informal walkthrough / troubleshoot guide detailing how the author 3D printed parts,

for any future students who might need this information. The author heavily recommends

reading the entire document, including the ‘what not to do’ section at the bottom of this

document.

These are the two thingiverse projects we used in order to create our quadrupedal robot.

https://www.thingiverse.com/thing:4937631

https://www.thingiverse.com/thing:4559827

Please contact the professor Dr. Vargas at noe.vargas@utrgv.edu who is responsible for the

Makerspace, where the 3D print lab is located. He will teach you about Makerspace printers,

which print faster than Creality printers but are not as accurate/precise. We had to use Creality

printers in order to get the parts in the correct geometries needed for this project.

Keep in mind shorts are not allowed in the Makerspace. Long-legged clothing only. No sandals,

only footwear that covers your entire foot.

You should also learn how to use Creality on your own time. For the splicer, the author used

Ultimaker Cura, which can be found here:

https://ultimaker.com/software/ultimaker-cura

Print settings for this splicer are located in the top right. The default infill is 20.0. The author

recommends 70.0 for parts undergoing significant load/tension/potential breaking points. 100.0

infill is possible, but please reserve this only for the parts undergoing the most amount of stress

and tension as 100.0 infill parts require a lot of filament. There is a larger difference in infill

quality from 20 to 50 than 70 to 100.

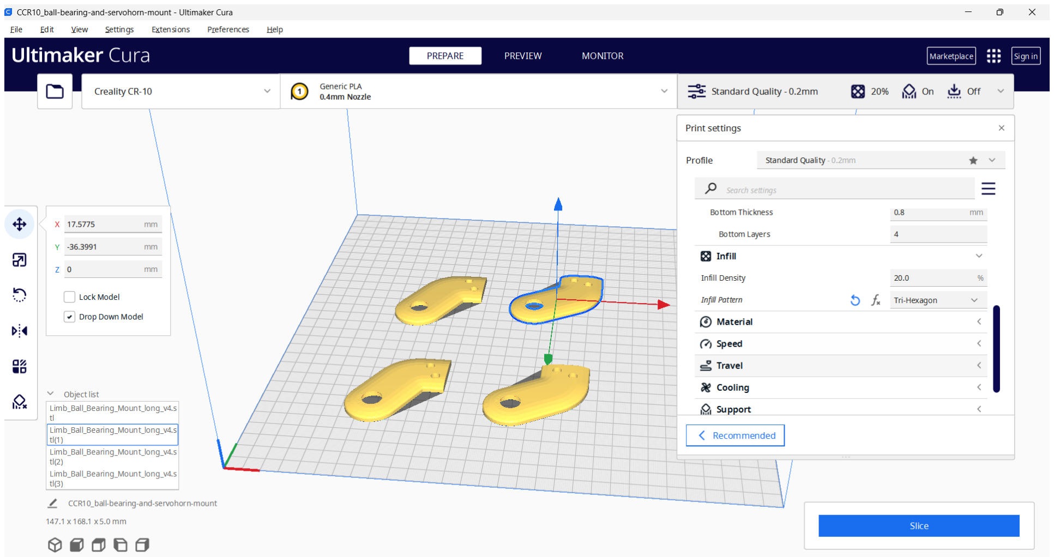
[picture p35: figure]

The higher the support overhead angle, the less supports will be printed. Less supports means

you have an easier time removing supports. More supports means your print is more likely to be

successful.

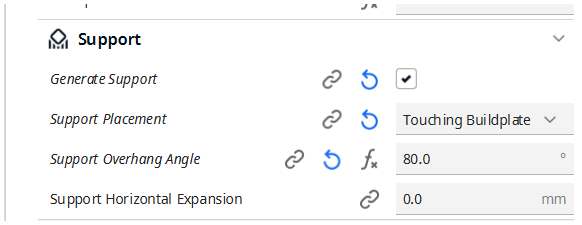
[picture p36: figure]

The Makerspace offers a variety of colors to print with, the author recommends just using

whatever color is ready to go.

The Makerspace offers a variety of materials to print with, the author recommends TPU for any

flexible parts and PLA otherwise. Other materials, like PETG are actually not as bend-resistant

as PLA for this project.

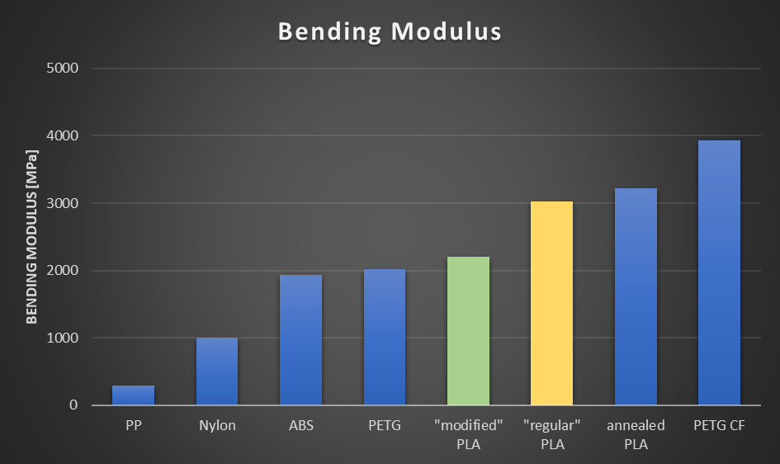
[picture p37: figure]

Please give this a quick read, where the above picture comes from.

https://www.cnckitchen.com/blog/the-difference-of-pla-and-pla-tested-feat-polymaker

Basically, the Bending Modulus is how much your material resists bending.

Please consult this bullet point list before each and every print:

- Make sure that ‘raft’ is selected in build plate adhesion, as this helps the Teaching

Assistants more easily remove the part from the print plate.

- Make sure that the printing temperature and build plate temperature are set to whatever

printer you are using. Most Creality printers use the same temperatures, but there is a

significant difference between certain printers, like Creality vs Makerbot.

- There is also a significant difference between materials. For example, TPU will

need different settings from PLA.

●

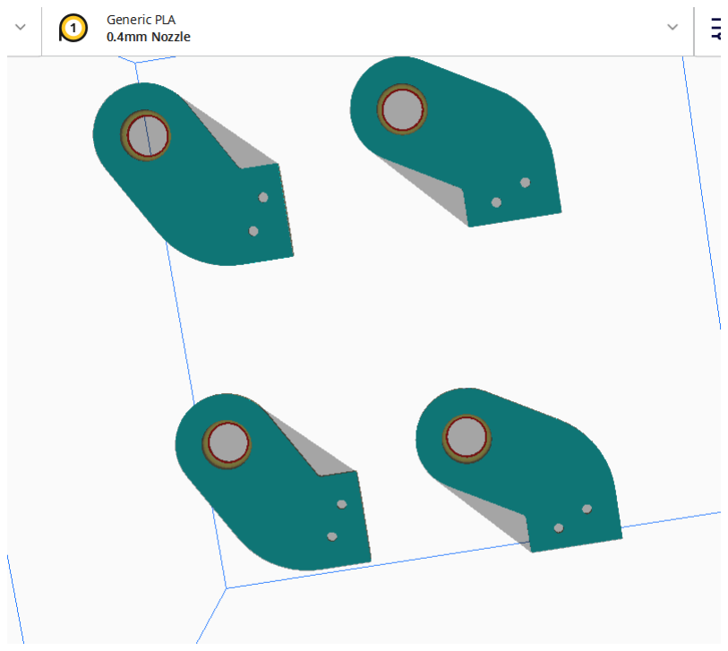
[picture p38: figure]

- Ensure that the bottom of each part is oriented correctly, we want as much of the

part touching the build plate as possible.

- ALWAYS CONSULT A TEACHING ASSISTANT BEFORE PRINTING!
- Specify desired printing material. Ask the assistant to check your settings.

After a print:

- Ask the Teaching Assistant to remove the parts from the print plate of a printer if you are

unable to do so yourself.

- Ask the Teaching Assistant to remove any supports/rafts that are difficult for you to

remove, it is better to ask an assistant than to accidentally break a part and have to waste

time and filament reprinting.

What not to do:

- Print a part that used the wrong material.

○

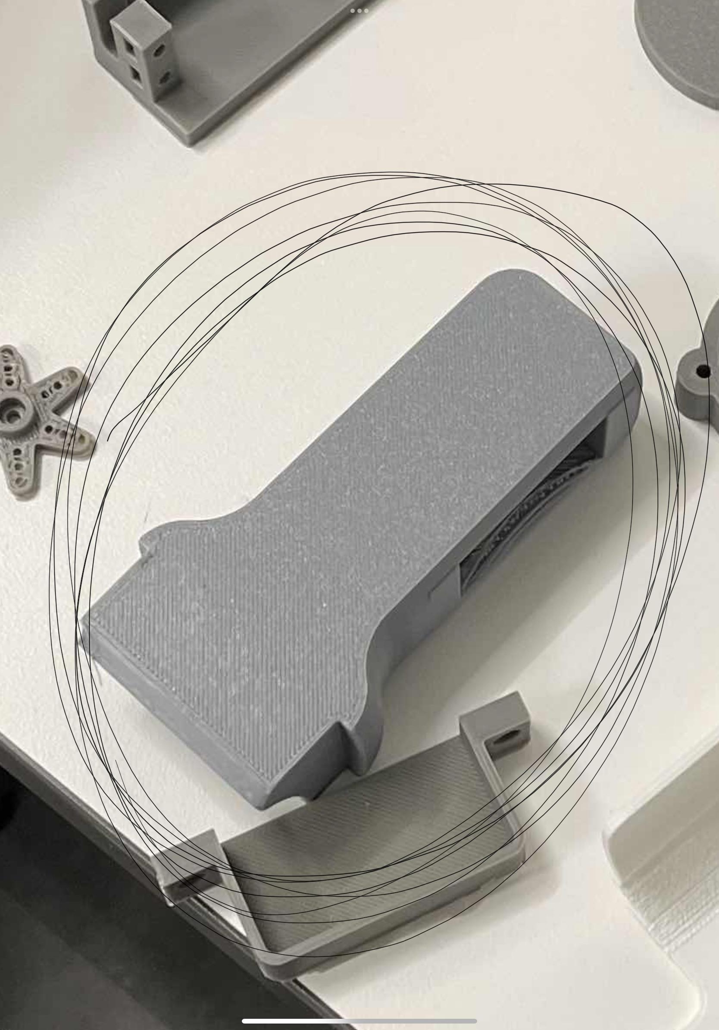
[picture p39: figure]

- Printed using TPU not PLA.

●

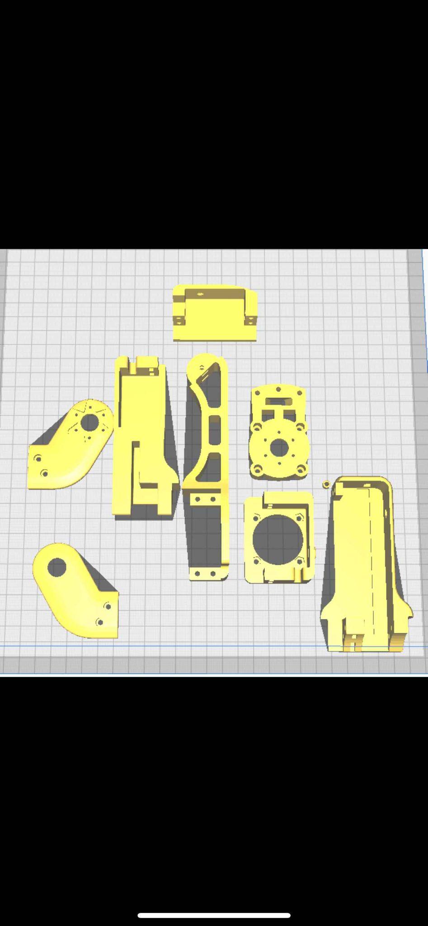
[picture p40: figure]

- This is a bad print destined to fail. Too many complex parts all at once. Parts are

too close together. For more complex parts, 4-5 on a single print board is the

maximum, and spread out more evenly that this example.

●

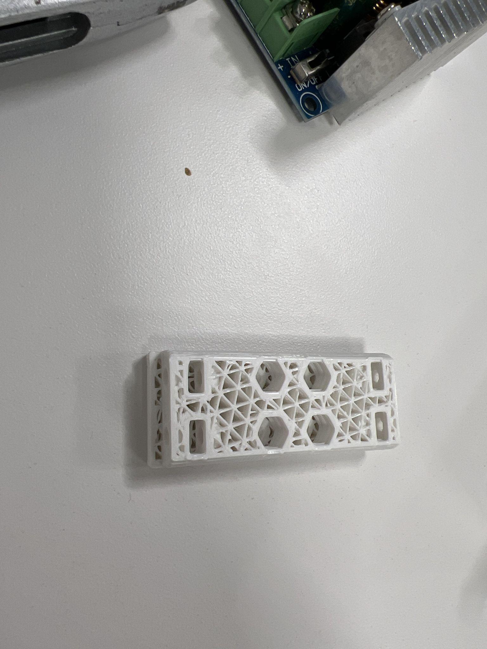
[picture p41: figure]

- Try to avoid grouping large and small items together. In the thingiverse files, there

is a Shoulder_Joint_Ball_Bearing_Pin_ stl file that is smaller than other parts. The

author tried printing this part alongside much larger parts. Since this pin was

finished printing on the print board earlier than the other parts, it cooled down,

and then fell off and messed up one of the axis on the printer. The Teaching

Assistants had to spend hours fixing the printer afterwards. Group larger parts

together, and smaller parts together. For the pin specifically, please try printing

these separately.

Finally, sometimes you’ll have leftover parts. For example, this next part isn’t necessarily printed

wrong, but we wanted this part printed again with a higher infill because we had to drill/insert

screws. Just keep these parts around for backup use.

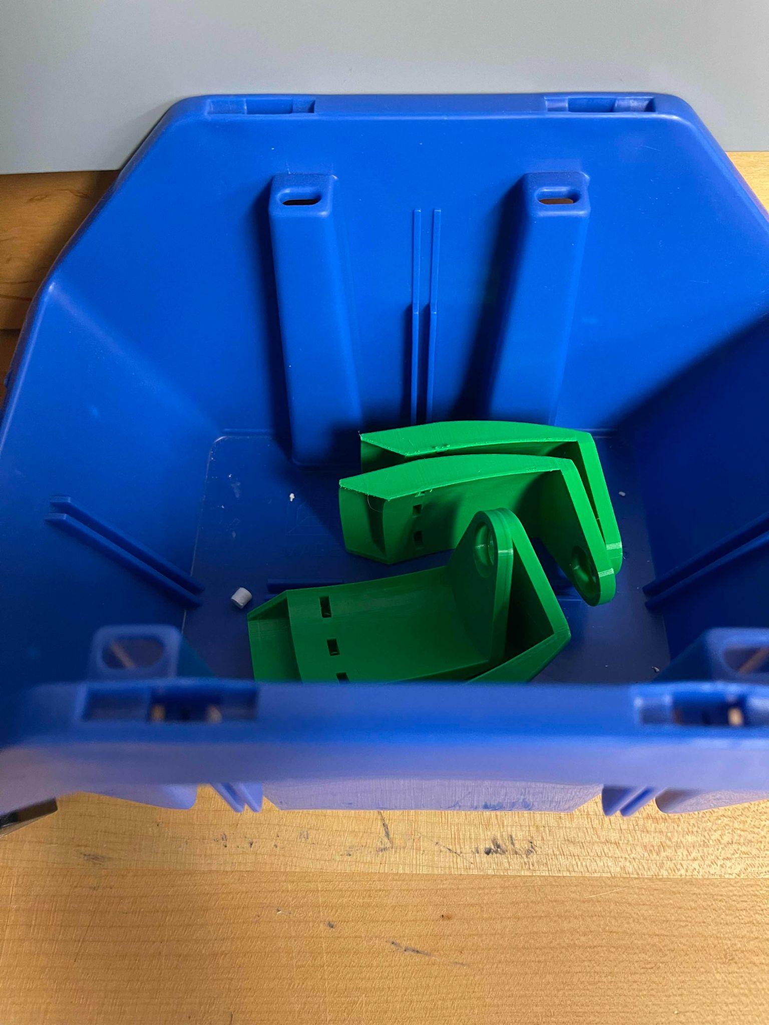
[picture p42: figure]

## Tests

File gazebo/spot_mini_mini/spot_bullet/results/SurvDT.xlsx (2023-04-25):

D^2-GMBC | GMBC | Open Loop
3802 | 4071 | 340
15204 | 50000 | 1588
50000 | 50000 | 194
3367 | 4786 | 273
50000 | 26405 | 725
50000 | 2355 | 823
50000 | 5567 | 433
3446 | 3081 | 1221
2494 | 2578 | 357
50000 | 3972 | 533
6809 | 49977 | 339
3977 | 5494 | 1047
956 | 8299 | 770
7736 | 48120 | 782
704 | 48799 | 1218
40140 | 1484 | 332
3098 | 4473 | 1822
10014 | 881 | 503
11279 | 46652 | 2586
50000 | 1778 | 386
50000 | 48347 | 475
6843 | 6573 | 3634
23521 | 21260 | 315
50000 | 37315 | 469
1540 | 2386 | 1514
35336 | 50000 | 2297
9770 | 46561 | 308
50000 | 50000 | 641
13982 | 14402 | 830
19027 | 1967 | 330
8197 | 1474 | 734
50000 | 8149 | 659
10019 | 13727 | 302
4039 | 1760 | 913
50000 | 47415 | 468
7830 | 12403 | 132
50000 | 8535 | 883
50000 | 5691 | 1146
2154 | 1693 | 1057
63 | 853 | 200
50000 | 1723 | 549
50000 | 10640 | 994
4701 | 2035 | 251
233 | 50000 | 221
50000 | 9030 | 458
38386 | 2968 | 400
50000 | 2175 | 216
32215 | 9069 | 1055
1874 | 296 | 569
45009 | 1466 | 1088
15273 | 7523 | 943
10127 | 1448 | 930
8888 | 2761 | 791
46 | 4069 | 693
50000 | 3054 | 413
50000 | 3675 | 329
50000 | 614 | 1124
15724 | 3735 | 625
50000 | 4152 | 1272
4553 | 46454 | 1374
50000 | 8953 | 846
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

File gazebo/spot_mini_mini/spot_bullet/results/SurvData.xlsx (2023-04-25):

GMBC NoRand | GMBC Rand | Vanilla
0.3761666334 | 2.566846387 | 0.4504933473
7.791723574 | 93.51027156 | 2.021946983
1.688631365 | 0.6597164398 | 0.2564869641
2.36367521 | 2.542091434 | 0.298872112
1.479152921 | 5.625441824 | 0.7747624704
0.3487126192 | 1.766385297 | 0.8614104187
71.46703521 | 3.199849575 | 0.331060141
2.790427193 | 3.376536067 | 1.365194468
2.150212923 | 1.384279117 | 0.4091254007
89.89775201 | 3.412237163 | 0.7626040445
3.842765019 | 100.0826394 | 0.480321771
3.849587376 | 4.757022207 | 0.8259271169
0.8209090785 | 8.730638477 | 0.8838849486
6.349937333 | 100.0794724 | 0.7101956963
0.9030301842 | 100.0811539 | 0.7970673578
7.436483122 | 1.547601007 | 0.2299096913
2.074093586 | 3.96058152 | 1.5969381
3.95411725 | 0.3899506402 | 0.3255577426
6.499229956 | 100.0908541 | 2.460069811
76.97402779 | 0.6840534713 | 0.5042259431
5.504716099 | 100.0828112 | 0.4550878285
5.85899765 | 3.374506636 | 3.222540597
5.93751101 | 7.424254466 | -0.004885771625
0.6327437231 | 7.633810088 | 0.2318684173
1.022627899 | 2.516190932 | 1.127472168
3.03744982 | 80.43125439 | 2.594159981
3.211506056 | 100.0818285 | 0.1319041376
85.22580041 | 53.87497664 | 0.7706576641
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

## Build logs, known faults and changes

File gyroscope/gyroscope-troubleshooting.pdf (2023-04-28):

This is an informal walkthrough / troubleshoot guide detailing how I got the gyroscope to work in ROS, for any future students who might need this information. Before following this guide, ensure that a catkin_ws workspace has already been created.

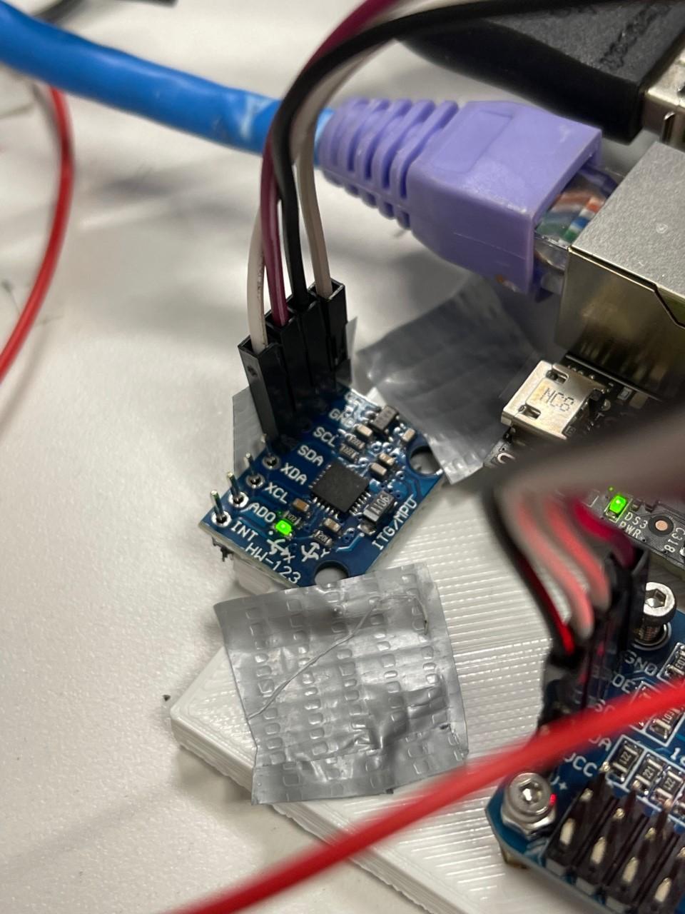
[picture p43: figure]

This is the physical gyroscope.

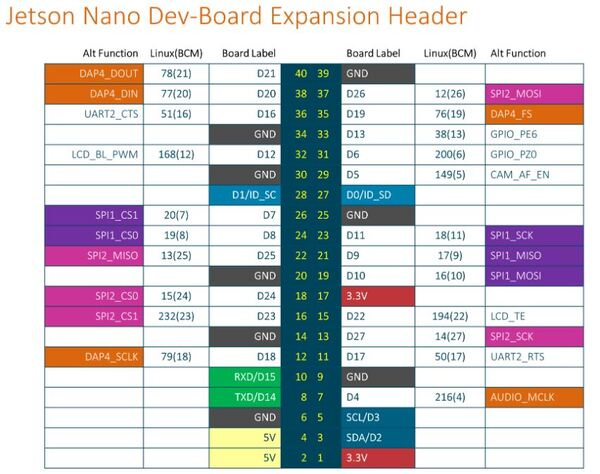
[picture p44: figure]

Please follow along with this tutorial: https://automaticaddison.com/visualize-imu-data-using-the-mpu6050-ros-and-jetson-nano/

and only follow Option 1: for both the starting programs and the ROS part of this tutorial.

Attach to the Jetson Nano using female-to-female jumper wires. The connection between the wire and the gyroscope is tenuous, the author heavily recommends soldering the gyroscope and/or the pins it comes with in order to avoid future issues.

Some diagrams will claim that there is an SCL/SDA pin in 27/28, but this is just false. No other pins will work besides pins 3 and 5 on a barebones Jetson Nano without any arduino.

If you run the command:

sudo i2cdetect -r -y 1 and the gyroscope is not being detected, you will have to make sure that all the wires are properly fitted and that the issue doesn’t lie with an incorrect pin configuration.

The next command I had issue with is:

pip3 install adafruit-blinka

where sometimes errors are thrown stating that the installation could not be completed. In this case you will have to uninstall any previous adafruit installations your teammates may have installed. Or, if that fails / you have issues, try the commands listed here:

https://github.com/facebook/prophet/issues/418

namely:

pip install --upgrade setuptools

sudo apt-get install python3.6-dev libmysqlclient-dev

Now, follow the automatic addison tutorial. The next error I encountered was when I tried running the second program:

Traceback (most recent call last):
File "mpu6050_simpletest.py", line 10, in <module>
mpu = adafruit_mpu6050.MPU6050(i2c)
File "/home/spotmicro/.local/lib/python3.8/site-packages/adafruit_mpu6050.py", line 205, in __init__
self.i2c_device = i2c_device.I2CDevice(i2c_bus, address)
File "/home/spotmicro/.local/lib/python3.8/site-packages/adafruit_bus_device/i2c_device.py", line 63, in __init__
self.__probe_for_device()
File "/home/spotmicro/.local/lib/python3.8/site-packages/adafruit_bus_device/i2c_device.py", line 185, in __probe_for_device
raise ValueError("No I2C device at address: 0x%x" % self.device_address)
ValueError: No I2C device at address: 0x68

If you get this error, this means that while adafruit-blinka is working your device is not showing up. The author used duct tape temporarily, as seen in the first photo in this guide, in order to fix the pins in place. Later, another teammate soldered the pins in place. Ensure not only that the light is on, but use the i2c detect command to ensure that the SCL/SDA pins are working properly.

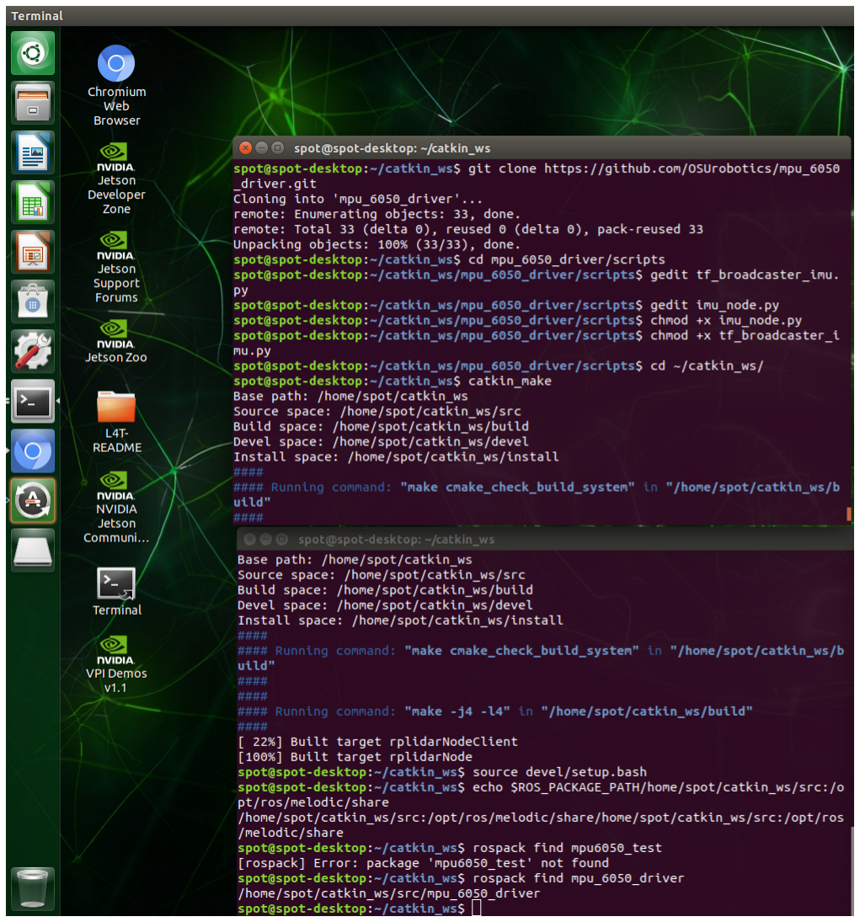
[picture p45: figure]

You should already have a catkin workspace if you installed ROS correctly.

Keep opening terminals as the automatic addison guide says to.

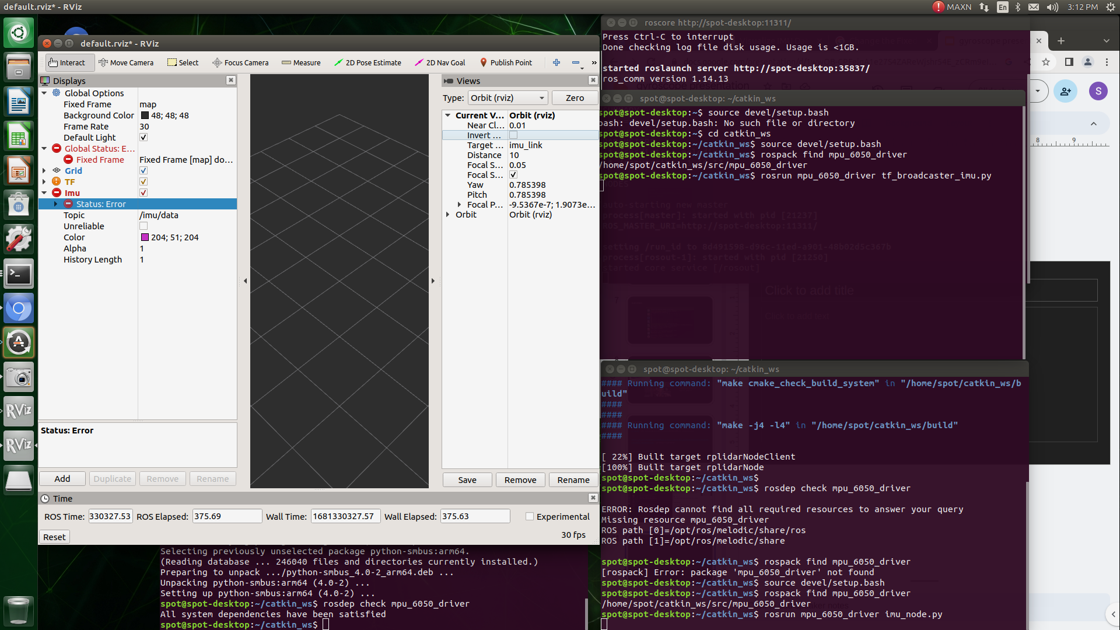
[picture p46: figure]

Around the part in the guide where it says to “Change the Fixed Frame parameter under Global Options to imu_link.”:

Some options will be drop down menus on the right of the .rviz file you just created.

Do not forget to Ctrl+C every single terminal once you are done, otherwise you run the risk of messing up critical files.

Helpful links:

https://automaticaddison.com/visualize-imu-data-using-the-mpu6050-ros-and-jetson-nano/
- Majority of work on the jetson nano / gyroscope implementation was done using this link.
- Also where the first image in this document comes from.
- Also has more information on physical implementation of gyroscope, including which head-to-head connections you will need.
- Last accessed April 13, 2023.

https://robotics.stackexchange.com/questions/9680/getting-rospack-package-not-found-error-in-r os (https://robotics.stackexchange.com/questions/9680/getting-rospack-package-not-found-error-in-ros)
- As soon as you open a terminal, type in source devel/setup.bash in order to make the ROS commands work properly. This is for all 9-12 terminals you’ll need to have up.
- Last accessed April 13, 2023.

https://github.com/facebook/prophet/issues/418
- Has commands that help fix a variety of pip command issues.
- Last accessed April 11, 2023.

https://www.odoo.com/forum/help-1/how-to-install-pip-in-python-3-on-ubuntu-18-04-167715
- pip installation for python 3 / ubuntu.
- Last accessed April 11, 2023.

https://github.com/NVIDIA/jetson-gpio
- Installing Jetson GPIO.
- Last accessed April 12, 2023.

https://answers.ros.org/question/353123/unable-to-locate-package-ros-noetic-desktop-full/
- Helpful docker commanders if you want to use ROS Noetic on ubuntu, however this is not recommended our team stuck with ROS Melodic.
- Last accessed April 12, 2023.

http://wiki.ros.org/melodic/Installation/Ubuntu
- ROS Melodic installation.
- Last accessed April 12, 2023.

http://wiki.ros.org/ROS/Tutorials/InstallingandConfiguringROSEnvironment
- Configuring the ROS environment, specifically maintaining a catkin_ws workspace.
- Last accessed April 12, 2023.

https://stackoverflow.com/questions/27053334/ros-package-not-found-after-catkin-make
- If ROS package doesn’t show using other commands.
- Last accessed April 12, 2023.

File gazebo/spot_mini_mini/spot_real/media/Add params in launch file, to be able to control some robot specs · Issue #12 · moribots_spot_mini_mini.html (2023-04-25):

Skip to content

(https://github.com/)



- In this repository All GitHub ↵
  Jump to ↵
- No suggested jump to results
- In this repository All GitHub ↵
  Jump to ↵
- In this repository All GitHub ↵
  Jump to ↵
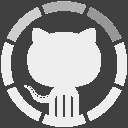
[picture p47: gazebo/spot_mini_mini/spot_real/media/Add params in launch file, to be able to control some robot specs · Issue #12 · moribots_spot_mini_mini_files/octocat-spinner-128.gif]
Octocat Spinner Icon
- 

(https://github.com/)

(https://github.com/notifications)

New repository (https://github.com/new) Import repository (https://github.com/new/import) New gist (https://gist.github.com/) New organization (https://github.com/organizations/new)

This repository

New issue (https://github.com/moribots/spot_mini_mini/issues/new/choose)

@moribots

Signed in as moribots (https://github.com/moribots)

turtle

working on robots!

### Edit status

turtle

Could not update your status, please try again.

80 remaining

#### Suggestions:

palm_tree

On vacation

face_with_thermometer

Out sick

house

Working from home

dart

Focusing

Busy

When others mention you, assign you, or request your review, GitHub will let them know that you have limited availability.

Clear status

Never

- Never
  Keep this status until you clear your status or edit your status.
- in 30 minutes
- in 1 hour
- in 4 hours
- today
- this week

Set status Clear status

Your profile (https://github.com/moribots) Your repositories (https://github.com/moribots?tab=repositories) Your organizations (https://github.com/settings/organizations) Your projects (https://github.com/moribots?tab=projects) Your stars (https://github.com/moribots?tab=stars) Your gists (https://gist.github.com/mine)

Feature preview

Help (https://docs.github.com/) Settings (https://github.com/settings/profile) Sign out

# moribots (https://github.com/moribots) / spot_mini_mini (https://github.com/moribots/spot_mini_mini)

- Unwatch
  Notifications
  Not watching Be notified only when participating or @mentioned. Watch
  Releases only Be notified of new releases, and when participating or @mentioned. Unwatch releases
  Watching Be notified of all conversations. Unwatch
  Ignoring Never be notified. Stop ignoring
  24 (https://github.com/moribots/spot_mini_mini/watchers)
- Unstar 271 (https://github.com/moribots/spot_mini_mini/stargazers) Star 271 (https://github.com/moribots/spot_mini_mini/stargazers)
- Fork

# Fork spot_mini_mini

  If this dialog fails to load, you can visit the fork page (https://github.com/moribots/spot_mini_mini/fork) directly.
  36 (https://github.com/moribots/spot_mini_mini/network/members)

Edit New issue (https://github.com/moribots/spot_mini_mini/issues/new/choose)

# Add params in launch file, to be able to control some robot specs #12

Save Cancel

Open

elpimous (https://github.com/elpimous) opened this issue 2 days ago · 2 comments

Open

# Add params in launch file, to be able to control some robot specs #12

elpimous (https://github.com/elpimous) opened this issue 2 days ago · 2 comments

## Comments

@elpimous (https://github.com/elpimous)

Pick your reaction

+1  smile tada thinking_face heart rocket eyes

Copy link Quote reply

Edit

Report content (https://github.com/contact/report-content?report=elpimous+%28user%29)

### elpimous (https://github.com/elpimous) commented 2 days ago

The use of params in ROS launchfile could help change some values in poses or walk specs :

robot height

Step Length

Step velocity

what policy model use.

Pick your reaction

+1  smile tada thinking_face heart rocket eyes

Select a reply ctrl .

The content you are editing has changed. Please copy your edits and refresh the page.

The use of params in ROS launchfile could help change some values in poses or walk specs : - robot height - Step Length - Step velocity - what policy model use. Attach files by dragging & dropping, selecting or pasting them.  Uploading your files… We don’t support that file type. Try again with a GIF, JPEG, JPG, PNG, DOCX, GZ, LOG, PDF, PPTX, TXT, XLSX or ZIP. Attaching documents requires write permission to this repository. Try again with a GIF, JPEG, JPG, PNG, DOCX, GZ, LOG, PDF, PPTX, TXT, XLSX or ZIP. We don’t support that file type. Try again with a GIF, JPEG, JPG, PNG, DOCX, GZ, LOG, PDF, PPTX, TXT, XLSX or ZIP. Yowza, that’s a big file Try again with a file smaller than 10MB. This file is empty. Try again with a file that’s not empty. This file is hidden. Try again with another file. Something went really wrong, and we can’t process that file. Try again. (https://guides.github.com/features/mastering-markdown/)

Nothing to preview

Update comment Cancel

@moribots (https://github.com/moribots)

Pick your reaction

+1  smile tada thinking_face heart rocket eyes

Copy link Quote reply

Reference in new issue

### Reference in new issue

Repository

spot_mini_mini

Repositories

Title

Body

Thanks Vincent! There is already a ros param for selecting your policy. Step length is controlled by pushing the right joystick forward, and step velocity is controlled by the bottom left and right bumpers (See README) I will add ones for your other requested features now. _Originally posted by @moribots in https://github.com/moribots/spot_mini_mini/issues/12#issuecomment-699081319_

Create issue

Edit Hide Delete

Report content (https://github.com/contact/report-content?report=moribots+%28user%29)

Owner

### moribots (https://github.com/moribots) commented 1 hour ago •

### edited

### Edited 1 time

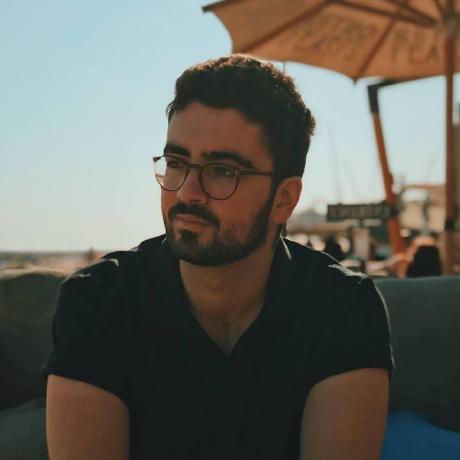
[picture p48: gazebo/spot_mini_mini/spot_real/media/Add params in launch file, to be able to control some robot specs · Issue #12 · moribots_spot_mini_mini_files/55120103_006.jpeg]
@moribots
###  moribots edited 43 minutes ago (most recent)

### @moribots moribots created 1 hour ago

### Choose a reason for hiding this comment

The reason will be displayed to describe this comment to others. Learn more (https://docs.github.com/articles/managing-disruptive-comments/#hiding-a-comment).

Hide comment

Thanks Vincent! There is already a ros param for selecting your policy. Step length is controlled by pushing the right joystick forward, and step velocity is controlled by the bottom left and right bumpers (See README)

I will add ones for your other requested features now.

Pick your reaction

+1  smile tada thinking_face heart rocket eyes

Select a reply ctrl .

The content you are editing has changed. Please copy your edits and refresh the page.

Thanks Vincent! There is already a ros param for selecting your policy. Step length is controlled by pushing the right joystick forward, and step velocity is controlled by the bottom left and right bumpers (See README) I will add ones for your other requested features now. Attach files by dragging & dropping, selecting or pasting them.  Uploading your files… We don’t support that file type. Try again with a GIF, JPEG, JPG, PNG, DOCX, GZ, LOG, PDF, PPTX, TXT, XLSX or ZIP. Attaching documents requires write permission to this repository. Try again with a GIF, JPEG, JPG, PNG, DOCX, GZ, LOG, PDF, PPTX, TXT, XLSX or ZIP. We don’t support that file type. Try again with a GIF, JPEG, JPG, PNG, DOCX, GZ, LOG, PDF, PPTX, TXT, XLSX or ZIP. Yowza, that’s a big file Try again with a file smaller than 10MB. This file is empty. Try again with a file that’s not empty. This file is hidden. Try again with another file. Something went really wrong, and we can’t process that file. Try again. (https://guides.github.com/features/mastering-markdown/)

Nothing to preview

Update comment Cancel

@elpimous (https://github.com/elpimous)

Pick your reaction

+1  smile tada thinking_face heart rocket eyes

Copy link Quote reply

Reference in new issue

### Reference in new issue

Repository

spot_mini_mini

Repositories

Title

Body

very reactive, Thanks Maurice ! _Originally posted by @elpimous in https://github.com/moribots/spot_mini_mini/issues/12#issuecomment-699097229_

Create issue

Edit Hide Delete

Report content (https://github.com/contact/report-content?report=elpimous+%28user%29)

Author

### elpimous (https://github.com/elpimous) commented 12 minutes ago

### Choose a reason for hiding this comment

The reason will be displayed to describe this comment to others. Learn more (https://docs.github.com/articles/managing-disruptive-comments/#hiding-a-comment).

Hide comment

very reactive, Thanks Maurice !

Pick your reaction

+1  smile tada thinking_face heart rocket eyes

Select a reply ctrl .

The content you are editing has changed. Please copy your edits and refresh the page.

very reactive, Thanks Maurice ! Attach files by dragging & dropping, selecting or pasting them.  Uploading your files… We don’t support that file type. Try again with a GIF, JPEG, JPG, PNG, DOCX, GZ, LOG, PDF, PPTX, TXT, XLSX or ZIP. Attaching documents requires write permission to this repository. Try again with a GIF, JPEG, JPG, PNG, DOCX, GZ, LOG, PDF, PPTX, TXT, XLSX or ZIP. We don’t support that file type. Try again with a GIF, JPEG, JPG, PNG, DOCX, GZ, LOG, PDF, PPTX, TXT, XLSX or ZIP. Yowza, that’s a big file Try again with a file smaller than 10MB. This file is empty. Try again with a file that’s not empty. This file is hidden. Try again with another file. Something went really wrong, and we can’t process that file. Try again. (https://guides.github.com/features/mastering-markdown/)

Nothing to preview

Update comment Cancel

@moribots (https://github.com/moribots)

Write Preview

Select a reply ctrl .

There was an error creating your Issue.

I've just made the changes. You can modify everything that contributes to Spot's motion in the `mini_ros/config/` directory ([link](https://github.com/moribots/spot_mini_mini/tree/spot/mini_ros/config)) Attach files by dragging & dropping, selecting or pasting them.  Uploading your files… We don’t support that file type. Try again with a GIF, JPEG, JPG, PNG, DOCX, GZ, LOG, PDF, PPTX, TXT, XLSX or ZIP. Attaching documents requires write permission to this repository. Try again with a GIF, JPEG, JPG, PNG, DOCX, GZ, LOG, PDF, PPTX, TXT, XLSX or ZIP. We don’t support that file type. Try again with a GIF, JPEG, JPG, PNG, DOCX, GZ, LOG, PDF, PPTX, TXT, XLSX or ZIP. Yowza, that’s a big file Try again with a file smaller than 10MB. This file is empty. Try again with a file that’s not empty. This file is hidden. Try again with another file. Something went really wrong, and we can’t process that file. Try again. (https://guides.github.com/features/mastering-markdown/)

Nothing to preview

Close with comment

Comment

Remember, contributions to this repository should follow its contributing guidelines (https://github.com/moribots/spot_mini_mini/blob/spot/CONTRIBUTING.md) and code of conduct (https://github.com/moribots/spot_mini_mini/blob/spot/CODE_OF_CONDUCT.md).

Assignees

Assign up to 10 people to this issue

You can only select 10 assignees.

Nothing to show

No one—assign yourself

Labels

Apply labels to this issue

None yet

Projects

Projects

None yet

Milestone

Set milestone

No milestone

Linked pull requests

Link a pull request from this repository

Successfully merging a pull request may close this issue.

None yet

Notifications

Customize

### Notification settings

Not subscribed

Only receive notifications from this issue when you have participated or have been @mentioned.

Subscribed

Receive all notifications from this issue.

Custom

You will only be notified for the events selected from the list below.
If you participate or are @mentioned you will be subscribed.

Closed

Receive a notification when this issue has been closed.

Reopened

Receive a notification when this issue has been reopened.

Save Cancel

Unsubscribe

You’re receiving notifications because you’re watching this repository.

2 participants

@elpimous (https://github.com/elpimous) @moribots (https://github.com/moribots)

Lock conversation

### Lock conversation on this issue

- Other users can’t add new comments to this issue.
- You and other collaborators with access (https://docs.github.com/articles/what-are-the-different-access-permissions) to this repository can still leave comments that others can see.
- You can always unlock this issue again in the future.

Reason for locking

Optionally, choose a reason for locking that others can see. Learn more about when it’s appropriate to lock conversations (https://docs.github.com/articles/locking-conversations).

Lock conversation on this issue

Pin issue

Transfer issue

### Transfer this issue

Choose a repository

Repositories

Transfer issue

Delete issue

#### Are you sure you want to delete this issue?

- This cannot be undone
- Only administrators can delete issues
- Deletion will remove the issue from search and previous references will point to a placeholder

Delete this issue

- © 2020 GitHub, Inc.
- Terms (https://github.com/site/terms)
- Privacy (https://github.com/site/privacy)
- Security (https://github.com/security)
- Status (https://githubstatus.com/)
- Help (https://docs.github.com/)

(https://github.com/)

- Contact GitHub (https://github.com/contact)
- Pricing (https://github.com/pricing)
- API (https://docs.github.com/)
- Training (https://services.github.com/)
- Blog (https://github.blog/)
- About (https://github.com/about)

You can’t perform that action at this time.

Author elpimous commented now very reactive, Thanks Maurice !

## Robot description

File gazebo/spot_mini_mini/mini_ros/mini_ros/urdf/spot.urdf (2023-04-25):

<?xml version="1.0" encoding="utf-8"?>
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
<robot name="spot">
  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
  <link name="base_link"/>
  <link name="base_inertia">
    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
    <inertial>
      <mass value="0.6"/>
      <origin rpy="0 0 0" xyz="0 0 0"/>
      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
    </inertial>
  </link>
  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
  <link name="battery">
    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
    <inertial>
      <mass value="0.4"/>
      <origin rpy="0 0 0" xyz="0 0 0"/>
      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
    </inertial>
  </link>
  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
  <link name="chassis_left">
    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
    <inertial>
      <mass value="0.01"/>
      <origin rpy="0 0 0" xyz="0 0 0"/>
      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
    </inertial>
  </link>
  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
  <link name="chassis_right">
    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
    <inertial>
      <mass value="0.01"/>
      <origin rpy="0 0 0" xyz="0 0 0"/>
      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
    </inertial>
  </link>
  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
  <link name="front">
    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
    <inertial>
      <mass value="0.1"/>
      <origin rpy="0 0 0" xyz="0 0 0"/>
      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
    </inertial>
  </link>
  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
  <link name="back">
    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
    <inertial>
      <mass value="0.1"/>
      <origin rpy="0 0 0" xyz="0 0 0"/>
      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
    </inertial>
  </link>
  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
  <link name="front_bracket">
    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
    <inertial>
      <mass value="0.1"/>
      <origin rpy="0 0 0" xyz="0 0 0"/>
      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
    </inertial>
  </link>
  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
  <link name="back_bracket">
    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
    <inertial>
      <mass value="0.1"/>
      <origin rpy="0 0 0" xyz="0 0 0"/>
      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
    </inertial>
  </link>
  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
  <link name="front_left_hip">
    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
    <inertial>
      <mass value="0.2"/>
      <origin rpy="0 0 0" xyz="0 0.075 0"/>
      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
    </inertial>
  </link>
  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
  <joint name="motor_front_left_hip" type="revolute">
    <axis xyz="1 0 0"/>
    <origin rpy="0 0 0" xyz="0.0915 0.0394 0.022"/>
    <parent link="front_bracket"/>
    <child link="front_left_hip"/>
    <limit effort="4.0" lower="-1.04" upper="1.04" velocity="4.0"/>
    <joint_properties damping="0.0" friction="0.0"/>
  </joint>
  <link name="front_left_upper_leg">
    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
    <inertial>
      <mass value="0.13"/>
      <origin rpy="0 0 0" xyz="-0.005 0.0175 -0.055"/>
      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
    </inertial>
  </link>
  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
  <joint name="motor_front_left_upper_leg" type="revolute">
    <axis xyz="0 1 0"/>
    <origin rpy="0 0 0" xyz="0.0015 0.045 -0.0087"/>
    <parent link="front_left_hip"/>
    <child link="front_left_upper_leg"/>
    <limit effort="4.0" lower="-1.57079632679" upper="2.59" velocity="4.0"/>
    <joint_properties damping="0.0" friction="0.0"/>
  </joint>
  <link name="front_left_lower_leg">
    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
    <inertial>
      <mass value="0.05"/>
      <origin rpy="0 0 0" xyz="-0.01 0 -0.06"/>
      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
    </inertial>
  </link>
  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
  <joint name="motor_front_left_lower_leg" type="revolute">
    <axis xyz="0 1 0"/>
    <origin rpy="0 0 0" xyz="-0.005 0.018 -0.109"/>
    <parent link="front_left_upper_leg"/>
    <child link="front_left_lower_leg"/>
    <limit effort="4.0" lower="-2.9" upper="1.57079632679" velocity="4.0"/>
    <joint_properties damping="0.0" friction="0.0"/>
  </joint>
  <link name="front_left_foot">
    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
    <inertial>
      <mass value="0.005"/>
      <origin rpy="0 0 0" xyz="0 0 0"/>
      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
    </inertial>
  </link>
  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
  <joint name="front_left_leg_foot" type="fixed">
    <origin rpy="0 0 0" xyz="0 0 -0.1265"/>
    <parent link="front_left_lower_leg"/>
    <child link="front_left_foot"/>
  </joint>
  <link name="back_left_hip">
    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
    <inertial>
      <mass value="0.2"/>
      <origin rpy="0 0 0" xyz="0 0.075 0"/>
      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
    </inertial>
  </link>
  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
  <joint name="motor_back_left_hip" type="revolute">
    <axis xyz="1 0 0"/>
    <origin rpy="0 0 0" xyz="-0.1365 0.0394 0.022"/>
    <parent link="back_bracket"/>
    <child link="back_left_hip"/>
    <limit effort="4.0" lower="-1.04" upper="1.04" velocity="4.0"/>
    <joint_properties damping="0.0" friction="0.0"/>
  </joint>
  <link name="back_left_upper_leg">
    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
    <inertial>
      <mass value="0.13"/>
      <origin rpy="0 0 0" xyz="-0.005 0.0175 -0.055"/>
      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
    </inertial>
  </link>
  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
  <joint name="motor_back_left_upper_leg" type="revolute">
    <axis xyz="0 1 0"/>
    <origin rpy="0 0 0" xyz="0.0015 0.045 -0.0087"/>
    <parent link="back_left_hip"/>
    <child link="back_left_upper_leg"/>
    <limit effort="4.0" lower="-1.57079632679" upper="2.59" velocity="4.0"/>
    <joint_properties damping="0.0" friction="0.0"/>
  </joint>
  <link name="back_left_lower_leg">
    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
    <inertial>
      <mass value="0.05"/>
      <origin rpy="0 0 0" xyz="-0.01 0 -0.06"/>
      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
    </inertial>
  </link>
  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
  <joint name="motor_back_left_lower_leg" type="revolute">
    <axis xyz="0 1 0"/>
    <origin rpy="0 0 0" xyz="-0.005 0.018 -0.109"/>
    <parent link="back_left_upper_leg"/>
    <child link="back_left_lower_leg"/>
    <limit effort="4.0" lower="-2.9" upper="1.57079632679" velocity="4.0"/>
    <joint_properties damping="0.0" friction="0.0"/>
  </joint>
  <link name="back_left_foot">
    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
    <inertial>
      <mass value="0.005"/>
      <origin rpy="0 0 0" xyz="0 0 0"/>
      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
    </inertial>
  </link>
  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
  <joint name="back_left_leg_foot" type="fixed">
    <origin rpy="0 0 0" xyz="0 0 -0.1265"/>
    <parent link="back_left_lower_leg"/>
    <child link="back_left_foot"/>
  </joint>
  <link name="front_right_hip">
    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
    <inertial>
      <mass value="0.2"/>
      <origin rpy="0 0 0" xyz="0 -0.075 0"/>
      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
    </inertial>
  </link>
  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
  <joint name="motor_front_right_hip" type="revolute">
    <axis xyz="1 0 0"/>
    <origin rpy="0 0 0" xyz="0.0915 -0.0394 0.022"/>
    <parent link="front_bracket"/>
    <child link="front_right_hip"/>
    <limit effort="4.0" lower="-1.04" upper="1.04" velocity="4.0"/>
    <joint_properties damping="0.0" friction="0.0"/>
  </joint>
  <link name="front_right_upper_leg">
    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
    <inertial>
      <mass value="0.13"/>
      <origin rpy="0 0 0" xyz="-0.005 -0.0175 -0.055"/>
      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
    </inertial>
  </link>
  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
  <joint name="motor_front_right_upper_leg" type="revolute">
    <axis xyz="0 1 0"/>
    <origin rpy="0 0 0" xyz="0.0015 -0.045 -0.0087"/>
    <parent link="front_right_hip"/>
    <child link="front_right_upper_leg"/>
    <limit effort="4.0" lower="-1.57079632679" upper="2.59" velocity="4.0"/>
    <joint_properties damping="0.0" friction="0.0"/>
  </joint>
  <link name="front_right_lower_leg">
    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
    <inertial>
      <mass value="0.05"/>
      <origin rpy="0 0 0" xyz="-0.01 0 -0.06"/>
      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
    </inertial>
  </link>
  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
  <joint name="motor_front_right_lower_leg" type="revolute">
    <axis xyz="0 1 0"/>
    <origin rpy="0 0 0" xyz="-0.005 -0.018 -0.109"/>
    <parent link="front_right_upper_leg"/>
    <child link="front_right_lower_leg"/>
    <limit effort="4.0" lower="-2.9" upper="1.57079632679" velocity="4.0"/>
    <joint_properties damping="0.0" friction="0.0"/>
  </joint>
  <link name="front_right_foot">
    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
    <inertial>
      <mass value="0.005"/>
      <origin rpy="0 0 0" xyz="0 0 0"/>
      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
    </inertial>
  </link>
  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
  <joint name="front_right_leg_foot" type="fixed">
    <origin rpy="0 0 0" xyz="0 0 -0.1265"/>
    <parent link="front_right_lower_leg"/>
    <child link="front_right_foot"/>
  </joint>
  <link name="back_right_hip">
    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
    <inertial>
      <mass value="0.2"/>
      <origin rpy="0 0 0" xyz="0 -0.075 0"/>
      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
    </inertial>
  </link>
  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
  <joint name="motor_back_right_hip" type="revolute">
    <axis xyz="1 0 0"/>
    <origin rpy="0 0 0" xyz="-0.1365 -0.0394 0.022"/>
    <parent link="back_bracket"/>
    <child link="back_right_hip"/>
    <limit effort="4.0" lower="-1.04" upper="1.04" velocity="4.0"/>
    <joint_properties damping="0.0" friction="0.0"/>
  </joint>
  <link name="back_right_upper_leg">
    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
    <inertial>
      <mass value="0.13"/>
      <origin rpy="0 0 0" xyz="-0.005 -0.0175 -0.055"/>
      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
    </inertial>
  </link>
  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
  <joint name="motor_back_right_upper_leg" type="revolute">
    <axis xyz="0 1 0"/>
    <origin rpy="0 0 0" xyz="0.0015 -0.045 -0.0087"/>
    <parent link="back_right_hip"/>
    <child link="back_right_upper_leg"/>
    <limit effort="4.0" lower="-1.57079632679" upper="2.59" velocity="4.0"/>
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

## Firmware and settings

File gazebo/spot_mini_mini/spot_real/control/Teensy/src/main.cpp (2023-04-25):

/// \file
/// \brief Teensy Main.

#include <Arduino.h>
#include <SpotServo.hpp>
#include <ContactSensor.hpp>
#include <Kinematics.hpp>
#include <Utilities.hpp>
#include <IMU.hpp>
#include <Servo.h>
#include <ROSSerial.hpp>

#define DEBUGSERIAL Serial

// NOTE: IMPORTANT - CALIBRATION VS RUN PARAMS
/* Instructions:
        - When assembling your servos, use NOMINAL_PWM mode, and be sure to enter the
          appropriate degree and pwm range too.
        - Use servo_calibration.launch on your Ubuntu machine running ROS Melodic and
          hence the servo_calibrator service to send PWM values to each joint, and then
          enter the resultant values in the Initialize() method of the SpotServo class.
        - STRAIGHT_LEGS, LIEDOWN, and PERPENDICULAR_LEGS are used to validate your calibraton.
        - RUN is used when you are finished calibrating, and are ready to run normal operations.
*/
enum MODE {NOMINAL_PWM, STRAIGHT_LEGS, LIEDOWN, PERPENDICULAR_LEGS, RUN};
MODE spot_mode = RUN;

bool ESTOPPED = false;
int viewing_speed = 400; // doesn't really mean anything, theoretically deg/sec
int walking_speed = 1500; // doesn't really mean anything, theoretically deg/sec
double last_estop = millis();
static unsigned long prev_publish_time;
const int ledPin = 13;


SpotServo FL_Shoulder, FL_Elbow, FL_Wrist, FR_Shoulder, FR_Elbow, FR_Wrist, BL_Shoulder, BL_Elbow, BL_Wrist, BR_Shoulder, BR_Elbow, BR_Wrist;
ContactSensor FL_sensor, FR_sensor, BL_sensor, BR_sensor;
SpotServo * Shoulders[4] = {&FL_Shoulder, &FR_Shoulder, &BL_Shoulder, &BR_Shoulder};
SpotServo * Elbows[4] = {&FL_Elbow, &FR_Elbow, &BL_Elbow, &BR_Elbow};
SpotServo * Wrists[4] = {&FL_Wrist, &FR_Wrist, &BL_Wrist, &BR_Wrist};
SpotServo * AllServos[12] = {&FL_Shoulder, &FL_Elbow, &FL_Wrist, &FR_Shoulder, &FR_Elbow, &FR_Wrist, &BL_Shoulder, &BL_Elbow, &BL_Wrist, &BR_Shoulder, &BR_Elbow, &BR_Wrist};
Utilities util;
Kinematics ik;
IMU imu_sensor;
LegType fl_leg = FL;
LegType fr_leg = FR;
LegType bl_leg = BL;
LegType br_leg = BR;
LegJoints FL_ = LegJoints(fl_leg);
LegJoints FR_ = LegJoints(fr_leg);
LegJoints BL_ = LegJoints(bl_leg);
LegJoints BR_ = LegJoints(br_leg);
ros_srl::ROSSerial ros_serial;

void update_servos()
{
    // ShoulderS
    FL_Shoulder.update_clk();
    FR_Shoulder.update_clk();
    BL_Shoulder.update_clk();
    BR_Shoulder.update_clk();

    // Elbow
    FL_Elbow.update_clk();
    FR_Elbow.update_clk();
    BL_Elbow.update_clk();
    BR_Elbow.update_clk();

    // WRIST
    FL_Wrist.update_clk();
    FR_Wrist.update_clk();
    BL_Wrist.update_clk();
    BR_Wrist.update_clk();
}

void command_servos(const LegJoints & legjoint, const bool & step_or_view = true)
{
  int leg = -1;

  if (legjoint.legtype == FL)
  {
    leg = 0;
  } else if (legjoint.legtype == FR)
  {
    leg = 1;
  } else if (legjoint.legtype == BL)
  {
    leg = 2;
  } else if (legjoint.legtype == BR)
  {
    leg = 3;
  }


  double shoulder_home = (*Shoulders[leg]).return_home();
  double elbow_home = (*Elbows[leg]).return_home();
  double wrist_home = (*Wrists[leg]).return_home();

  double Shoulder_angle = util.angleConversion(legjoint.shoulder, shoulder_home, legjoint.legtype, Shoulder);
  double Elbow_angle = legjoint.elbow;
  double Wrist_angle = legjoint.wrist;

  double s_dist = abs(Shoulder_angle - (*Shoulders[leg]).GetPoseEstimate());
  double e_dist = abs(Elbow_angle - (*Elbows[leg]).GetPoseEstimate());
  double w_dist = abs(Wrist_angle - (*Wrists[leg]).GetPoseEstimate());

  double scaling_factor = util.max(s_dist, e_dist, w_dist);

  s_dist /= scaling_factor;
  e_dist /= scaling_factor;
  w_dist /= scaling_factor;

  double s_speed = 0.0;
  double e_speed = 0.0;
  double w_speed = 0.0;

  if (step_or_view)
  {
    s_speed = viewing_speed * s_dist;
    s_speed = max(s_speed, viewing_speed / 10.0);
    e_speed = viewing_speed * e_dist;
    e_speed = max(e_speed, viewing_speed / 10.0);
    w_speed = viewing_speed * w_dist;
    w_speed = max(w_speed, viewing_speed / 10.0);
  } else
  {
    s_speed = walking_speed * s_dist;
    e_speed = walking_speed * e_dist;
    w_speed = walking_speed * w_dist;
  }

  (*Shoulders[leg]).SetGoal(Shoulder_angle, s_speed, step_or_view);
  (*Elbows[leg]).SetGoal(Elbow_angle, e_speed, step_or_view);
  (*Wrists[leg]).SetGoal(Wrist_angle, w_speed, step_or_view);
  
}

void update_sensors()
{
    FL_sensor.update_clk();
    FR_sensor.update_clk();
    BL_sensor.update_clk();
    BR_sensor.update_clk();
}

void set_stance(const double & f_shoulder_stance = 0.0, const double & f_elbow_stance = 0.0, const double & f_wrist_stance = 0.0,
                const double & r_shoulder_stance = 0.0, const double & r_elbow_stance = 0.0, const double & r_wrist_stance = 0.0)
{
  // Legs
  FL_.FillLegJoint(f_shoulder_stance, f_elbow_stance, f_wrist_stance);
  FR_.FillLegJoint(f_shoulder_stance, f_elbow_stance, f_wrist_stance);
  BL_.FillLegJoint(r_shoulder_stance, r_elbow_stance, r_wrist_stance);
  BR_.FillLegJoint(r_shoulder_stance, r_elbow_stance, r_wrist_stance);

  command_servos(FL_);
  command_servos(FR_);
  command_servos(BL_);
  command_servos(BR_);

  // Loop until goal reached - check BR Wrist (last one)
  while (!BR_Wrist.GoalReached())
  {
    update_servos();
  }
}


// Set servo pwm values to nominal assuming 500~2500 range and 270 degree servos.
void nominal_servo_pwm(const double & servo_range = 270, const int & min_pwm = 500, const int & max_pwm = 2500)
{
  // Attach motors for assembly
  // Shoulders
  FL_Shoulder.AssemblyInit(2, min_pwm, max_pwm);
  FR_Shoulder.AssemblyInit(5, min_pwm, max_pwm);
  BL_Shoulder.AssemblyInit(8, min_pwm, max_pwm);
  BR_Shoulder.AssemblyInit(11, min_pwm, max_pwm);
  
  //Elbows
  FL_Elbow.AssemblyInit(3, min_pwm, max_pwm);
  FR_Elbow.AssemblyInit(6, min_pwm, max_pwm);
  BL_Elbow.AssemblyInit(9, min_pwm, max_pwm);
  BR_Elbow.AssemblyInit(12, min_pwm, max_pwm);

  //Wrists
  FL_Wrist.AssemblyInit(4, min_pwm, max_pwm);
  FR_Wrist.AssemblyInit(7, min_pwm, max_pwm);
  BL_Wrist.AssemblyInit(10, min_pwm, max_pwm);
  BR_Wrist.AssemblyInit(13, min_pwm, max_pwm);

  // halfway for shoulder and elbow
  int halfway_pulse = round(0.5 * (max_pwm - min_pwm) + min_pwm); // 1500
  int shoulder_pulse = halfway_pulse; // 1500
  int elbow_pulse = halfway_pulse; // 1500

  // wrists need roughly 180
  int remaining_range = round(((180.0 - (servo_range / 2.0)) / double(servo_range)) * (max_pwm - min_pwm));
  int left_wrist_pulse = halfway_pulse - remaining_range; // 1167
  int right_wrist_pulse = halfway_pulse + remaining_range; // 1833
  //FL
  AllServos[0]->writePulse(shoulder_pulse);
  AllServos[1]->writePulse(elbow_pulse);
  AllServos[2]->writePulse(left_wrist_pulse);
  //FR
  AllServos[3]->writePulse(shoulder_pulse);
  AllServos[4]->writePulse(elbow_pulse);
  AllServos[5]->writePulse(right_wrist_pulse);
  //BL
  AllServos[6]->writePulse(shoulder_pulse);
  AllServos[7]->writePulse(elbow_pulse);
  AllServos[8]->writePulse(left_wrist_pulse);
  //BR
  AllServos[9]->writePulse(shoulder_pulse);
  AllServos[10]->writePulse(elbow_pulse);
  AllServos[11]->writePulse(right_wrist_pulse);
}

void run_sequence()
{
  // Move to Crouching Stance
  delay(2000);
  double f_shoulder_stance = 0.0;
  double f_elbow_stance =  36.13;
  double f_wrist_stance = -75.84;
  double r_shoulder_stance = 0.0;
  double r_elbow_stance =  36.13;
  double r_wrist_stance = -75.84;
  set_stance(f_shoulder_stance, f_elbow_stance, f_wrist_stance, r_shoulder_stance, r_elbow_stance, r_wrist_stance);
}

void straight_calibration_sequence()
{
  set_stance();
}

void lie_calibration_sequence()
{

  // Move to Extended stance
  delay(2000);
  double shoulder_stance = 0.0;
  double elbow_stance =  90.0;
  double wrist_stance = -170.3;
  set_stance(shoulder_stance, elbow_stance, wrist_stance, shoulder_stance, elbow_stance, wrist_stance);

}

void perpendicular_calibration_sequence()
{

  // Move to Extended stance
  delay(2000);
  set_stance();
  // Move to Extended stance
  delay(10000);
  double shoulder_stance = 0.0;
  double elbow_stance =  90.0;
  double wrist_stance = -90.0;
  set_stance(shoulder_stance, elbow_stance, wrist_stance, shoulder_stance, elbow_stance, wrist_stance);

}

// THIS ONLY RUNS ONCE
void setup()
{

  Serial.begin(9600);

  // NOTE: See top of file for spot_mode explanation:
  // ONLY USE THIS MODE DURING ASSEMBLY
  if (spot_mode == NOMINAL_PWM)
  {
    // Neutral Setting
    nominal_servo_pwm();
    // Prevent Servo Updates
    ESTOPPED = true;
  } else 
  {

    // IK - unused
    ik.Initialize(0.04, 0.1, 0.1);

    // SERVOS: Pin, StandAngle, HomeAngle, Offset, LegType, JointType, min_pwm, max_pwm, min_pwm_angle, max_pwm_angle
    // Shoulders
    double shoulder_liedown = 0.0;
    FL_Shoulder.Initialize(2, 135 + shoulder_liedown, 135, -7.25, FL, Shoulder, 500, 2400); // 0 | 0: STRAIGHT | 90: OUT | -90 IN
    FR_Shoulder.Initialize(5, 135 - shoulder_liedown, 135, -5.5, FR, Shoulder, 500, 2400);  // 1 | 0: STRAIGHT | 90: IN  | -90 OUT
    BL_Shoulder.Initialize(8, 135 + shoulder_liedown, 135, 5.75, BL, Shoulder, 500, 2400);  // 2 | 0: STRAIGHT | 90: OUT | -90 IN
    BR_Shoulder.Initialize(11, 135 - shoulder_liedown, 135, -4.0, BR, Shoulder, 500, 2400); // 3 | 0: STRAIGHT | 90: IN  | -90 OUT
    
    //Elbows
    double elbow_liedown = 90.0;
    FL_Elbow.Initialize(3, elbow_liedown, 0, 0.0, FL, Elbow, 1410, 2062, 0.0, 90.0);        // 4 | 0: STRAIGHT | 90: BACK
    FR_Elbow.Initialize(6, elbow_liedown, 0, 0.0, FR, Elbow, 1408, 733, 0.0, 90.0);         // 5 | 0: STRAIGHT | 90: BACK
    BL_Elbow.Initialize(9, elbow_liedown, 0, 0.0, BL, Elbow, 1460, 2095, 0.0, 90.0);        // 6 | 0: STRAIGHT | 90: BACK
    BR_Elbow.Initialize(12, elbow_liedown, 0, 0.0, BR, Elbow, 1505, 850, 0.0, 90.0);        // 7 | 0: STRAIGHT | 90: BACK

    //Wrists
    double wrist_liedown = -160.0;
    FL_Wrist.Initialize(4, wrist_liedown, 0, 0.0, FL, Wrist, 1755, 2320, -90.0, -165.0);    // 8 | 0: STRAIGHT | -90: FORWARD
    FR_Wrist.Initialize(7, wrist_liedown, 0, 0.0, FR, Wrist, 1805, 1150, 0.0, -90.0);       // 9 | 0: STRAIGHT | -90: FORWARD
    BL_Wrist.Initialize(10, wrist_liedown, 0, 0.0, BL, Wrist, 1100, 1733, 0.0, -90.0);     // 10 | 0: STRAIGHT | -90: FORWARD
    BR_Wrist.Initialize(13, wrist_liedown, 0, 0.0, BR, Wrist, 1788, 1153, 0.0, -90.0);     // 11 | 0: STRAIGHT | -90: FORWARD

    // Contact Sensors
    FL_sensor.Initialize(A9, 17);
    FR_sensor.Initialize(A8, 16);
    BL_sensor.Initialize(A7, 15);
    BR_sensor.Initialize(A6, 14);

    // IMU
    imu_sensor.Initialize();

    // NOTE: See top of file for spot_mode explanation:
    if (spot_mode == STRAIGHT_LEGS)
    {
      straight_calibration_sequence();
    } else if (spot_mode == LIEDOWN)
    {
      lie_calibration_sequence();
    } else if (spot_mode == PERPENDICULAR_LEGS)
    {
      perpendicular_calibration_sequence();
    } else
    {
      run_sequence();
    }
  }

  last_estop = millis();

  prev_publish_time = micros();
}

// THIS LOOPS FOREVER
void loop()
{
  // CHECK SENSORS AND SEND INFO
  // CONTACT
  // 1'000'000 / 20'000 = 50hz
  if ((micros() - prev_publish_time) >= 20000)
  {
    ros_serial.publishContacts(FL_sensor.isTriggered(), FR_sensor.isTriggered(), BL_sensor.isTriggered(), BR_sensor.isTriggered());

    //IMU
    if (imu_sensor.available())
    {
      imu::Vector<3> eul = imu_sensor.GetEuler();
      imu::Vector<3> acc = imu_sensor.GetAcc();
      imu::Vector<3> gyro = imu_sensor.GetGyro();

      ros_serial.publishIMU(eul, acc, gyro);
    }

    prev_publish_time = micros();
  }

  // Only allow controller commands if not E-STOPPED
  // Direct pulse commands from calibration still allowed.
  if(!ESTOPPED)
  {
    update_servos();
  }

  // Update Sensors
  update_sensors();
  
  // Command Servos
  if (ros_serial.jointsInputIsActive())
  {
    bool step_or_view = false;
    ros_serial.returnJoints(FL_, FR_, BL_, BR_, step_or_view);
    command_servos(FL_, step_or_view);
    command_servos(FR_, step_or_view);
    command_servos(BL_, step_or_view);
    command_servos(BR_, step_or_view);
  } else if (ros_serial.jointsPulseIsActive())
  {
    int servo_num = ros_serial.returnServoNum();
    int pulse = ros_serial.returnPulse();

    if (servo_num > -1 and servo_num < 12)
    {
      AllServos[servo_num]->writePulse(pulse);
    }

    ros_serial.resetPulseTopic();
  }

  // Update ROS Node (spinOnce etc...)
  ros_serial.run();
}
